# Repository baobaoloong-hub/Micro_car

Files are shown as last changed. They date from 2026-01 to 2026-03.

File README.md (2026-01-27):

# Micro_car
### gitee上传不了
#### 写在前面
前几个月抽了点时间画的车模，还想着再打一年，可惜要考研没时间，而且也没队友一起玩了，直接开源了,负压部分随便画的(效果挺好7w功率1.2kg+,同功率没见到比这个高的了),车模优化空间很大,自行探索,车模除了负压部分，不需要 3d 打印，所以车模很精致，而且挺稳定的，非常易上手
#⚠️注意⚠️
仅供参考，觉得不行的就当看个乐，毕竟我没下过地跑过，也希望有佬能参考做完，记得让我饱饱眼福，祝21届各位一路开挂，斩获佳绩，赛出风采！

#### 说明
1. 编码器测试过是可以的，`编码器磁铁和电机靠的有些近会有一些的小影响，自制编码器没什么难点，一个磁编码器芯片，需要输出方向正交编码器加个 d 触发器就可以了，可以试试英飞凌的 tle5012，e1000 版本的，出厂默认正交输出（手册好像写的 4096 线），也可以使用其他的比如 mt6835...

2. 电机选型(预留了10mm,12mm孔位,其他的自行修改)，没细找电机，直接无脑 030 ,最好是铷磁铁的，扭力要大（折线需要大扭力，尤其是直角，有时候跑不快，上限低大概率是电机没劲）,牛爷爷用的那个也挺好，就是略微有点重。有实力的佬挑战一下无刷，好盈 1625，一些蚊车电机，淘宝还有好多不知名的好电机，钞能力直接马克松冯哈勃，二手的不推荐,好多都是快坏了的

3. 裙边，材质自己挑，铁氟龙的看过学弟的，感觉偏硬，容易变形，没用过不评价,用过的可以说说，推荐那种大棚膜，2 平米 2.6 元，四舍五入就是白送！根本用不完，耐磨还有韧性不易形变，强推强推，还有就是贴膜，直接纳米胶，大块的铺，尽量铺宽一点，不要留缝防止漏气，可以参考我给的图片。

4. 负压...

5. 开启负压后车模变形，轮子出现外八问题，不一定要觉得是底板硬度不够，可以再上面加个支撑，这个支撑可以是你的 板子，也可以任何东西，参考我去年的车模结构，底板我有打过铝基板，单层正好能放开电源和三个电机的驱动，1.5mm 板很重，20g 整，有佬有空可以试试 1mm 或者换成普通的板子。还有，飞檐走壁不知道底盘是不是有点低，自行调整（我感觉没大问题）

6. 胎皮，省事直接买的成品，很好用，推荐一下牛爷爷的硅胶贴包海绵（牛爷爷群里有）和青山佬的世一胎皮，

7. 3d 打印部分，我用的竹子的 a1mini，打印部分只有扇叶和负压支架，一定要开圆孔补偿，可以轻松装上且扇叶不松动，想要减轻重量轮毂也可以打印。
关于负压电机的那个支架，可以改进一下，换成弹簧型那种，我看到过国外的鼠车并不是直接连接，好像因为扇叶动平衡不好，会震动，螺丝共振会松动，陀螺仪可能也会漂，有条件的陀螺仪也加一下减震柱，类似穿越机（可能有点多此一举），不过这些问题我还没有发现车模也没感觉到震动

8. 关于车模的测试，我是建议大家一步到位，能用碳板用碳板，不要用 3 d 打印，因为很多问题是当你换了稳定的材质才发现根本没那回事，尤其是负压和底板摩擦，一套碳板大概 40 左右甚至更低，不想花钱直接打 pcb 替代碳板（比赛哪有不花钱的）

9. 待补充...

#### 物料清单

| 物品  | 店铺 | 备注 | |
|----|---|---|---|
| 轮毂 | 叮叮玩具城 | 中径,店铺里款式颜色很多自行选择 |  https://e.tb.cn/h.7KCqEZDSIRYSRkK?tk=ES7zUhpZbzG |
| 胎皮 | 龙祥兴 | 硅胶套皮  | https://e.tb.cn/h.7KaQ1hg8XNjvOgW?tk=3CPaUhpYhlx  |
| 径向磁铁  | 年磁科技 |  径向!!!!!! | https://e.tb.cn/h.7KlAtBGKxQvzEUj?tk=V5gjUhpasUc  |
| 轴套 | 2*4*6 |  不是必须买 | |
| 尼龙柱 | 6或7  | 负压用  | |
| 防滑螺母m2 | | | |
| 0.5模齿轮 | 大家一起来数牙 , 玩具齿轮大全 , 自己打印 | 轮齿40,电机齿14(自行调整,加起来54就行) ||
| 碳板 | | | |  | |  |
| 法兰轴承*8 | | F682w1.5 | |  | | https://e.tb.cn/h.7KO1xlum2gcvA1G?tk=EAH1Uhp14ll |
| m2螺丝  | | 18,20,22(具体自行调整,有条件的直接钛合金 | |  | |  |
| 8520或8523 | | | |
| 六面螺母 | | 6*6*6  |  https://e.tb.cn/h.7KOXKpCuhlABRpd?tk=7vObUhpcHJm |
| ... | | | |

#### 安装说明

看着文件装吧.

#### 参与贡献

1.  Fork 本仓库
2.  新建 Feat_xxx 分支
3.  提交代码
4.  新建 Pull Request

#### 特技

1.  使用 Readme\_XXX.md 来支持不同的语言，例如 Readme\_en.md, Readme\_zh.md
2.  Gitee 官方博客 [blog.gitee.com](https://blog.gitee.com)
3.  你可以 [https://gitee.com/explore](https://gitee.com/explore) 这个地址来了解 Gitee 上的优秀开源项目
4.  [GVP](https://gitee.com/gvp) 全称是 Gitee 最有价值开源项目，是综合评定出的优秀开源项目
5.  Gitee 官方提供的使用手册 [https://gitee.com/help](https://gitee.com/help)
6.  Gitee 封面人物是一档用来展示 Gitee 会员风采的栏目 [https://gitee.com/gitee-stars/](https://gitee.com/gitee-stars/)

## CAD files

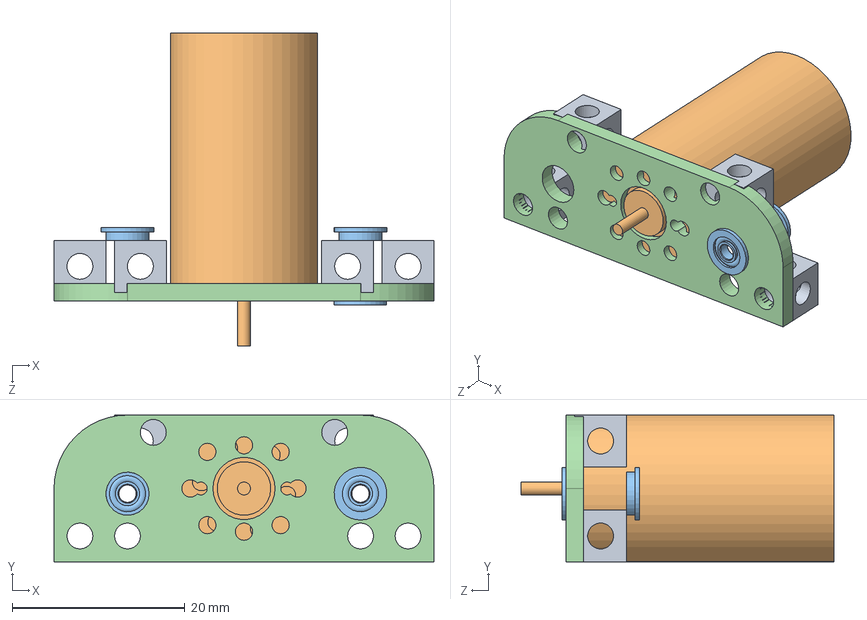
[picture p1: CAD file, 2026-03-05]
更新_看这个/侧轮整体.SLDASM
44.0 x 17.0 x 36.2 mm
侧板
F682-2Z 2×5×1.5_法兰轴承 x 3
六面螺母 x 4

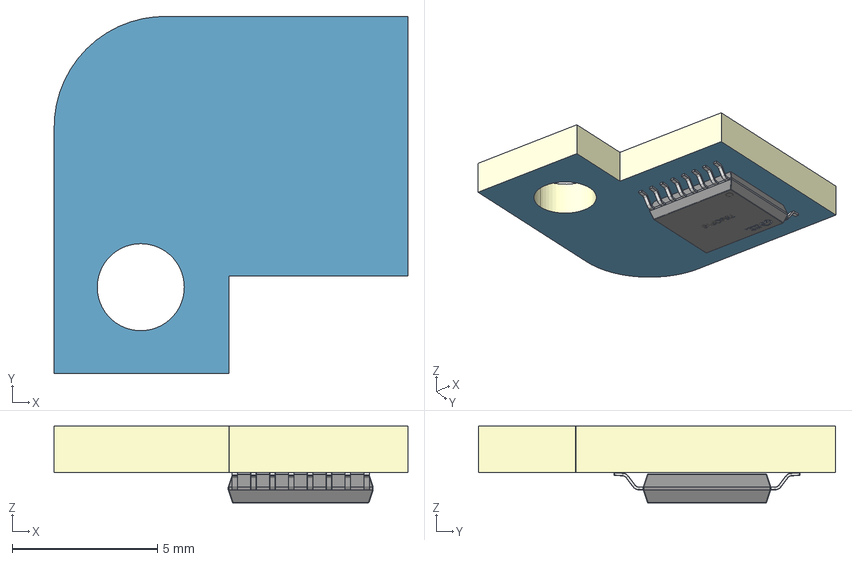
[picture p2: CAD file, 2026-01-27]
编码器.step
12.2 x 12.3 x 2.65 mm
Board~ZMgj
TopCopper~ZMgj
BottomCopper~ZMgj
TopFpcStiffener~ZMgj
BottomFpcStiffener~ZMgj
TSSOP-16_L5.0-W4.4-P0.65-LS6.4-BL~TSSOP-16_ L5.0-W4.4-H1.0-LS6.4-P0.65~ZMgj

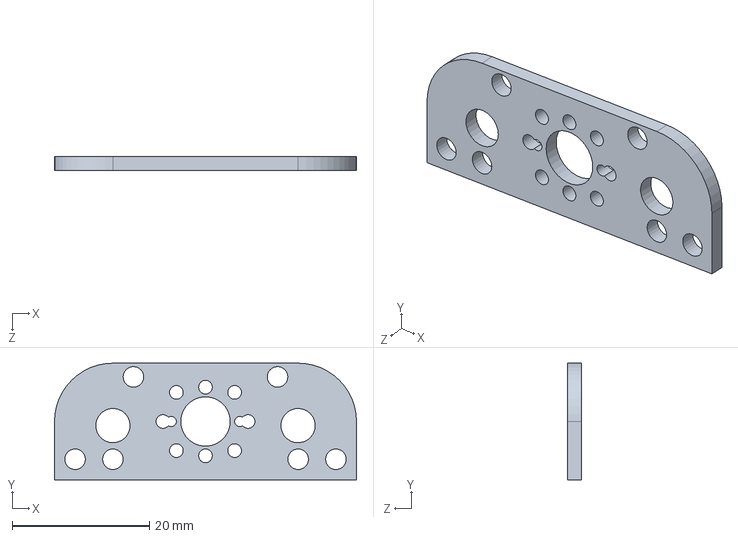
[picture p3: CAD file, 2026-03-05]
更新_看这个/侧板.SLDPRT
44.0 x 17.0 x 2.00 mm

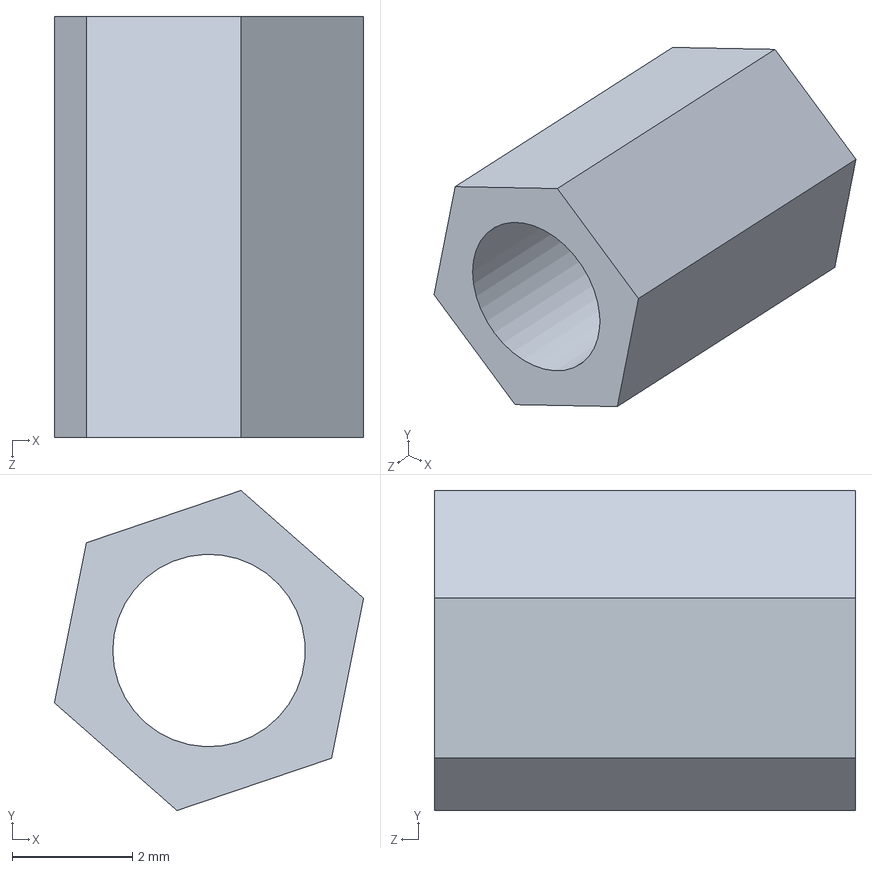
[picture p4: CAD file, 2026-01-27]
更新_看这个/铜柱7mm.SLDPRT
5.14 x 5.32 x 7.00 mm

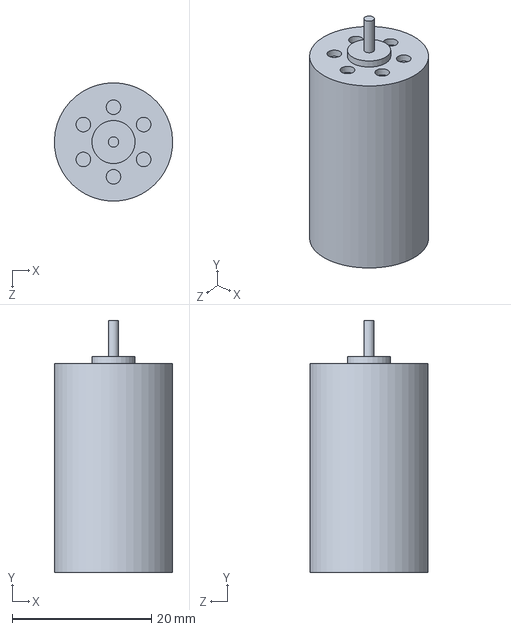
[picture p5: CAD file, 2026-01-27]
更新_看这个/1725.SLDPRT
17.0 x 36.2 x 17.0 mm

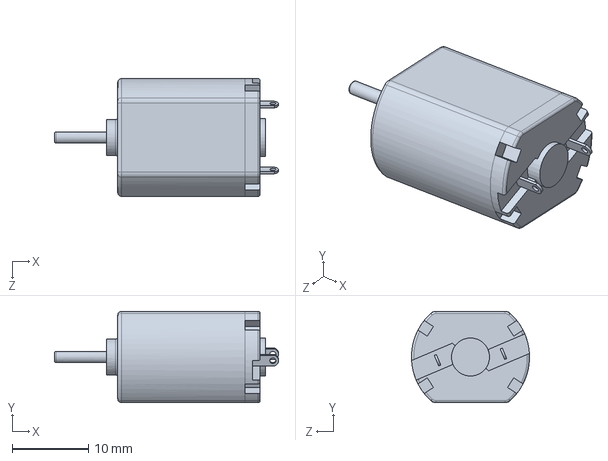
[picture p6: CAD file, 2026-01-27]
更新_看这个/Standard Motor 030.SLDPRT
29.4 x 12.0 x 15.5 mm

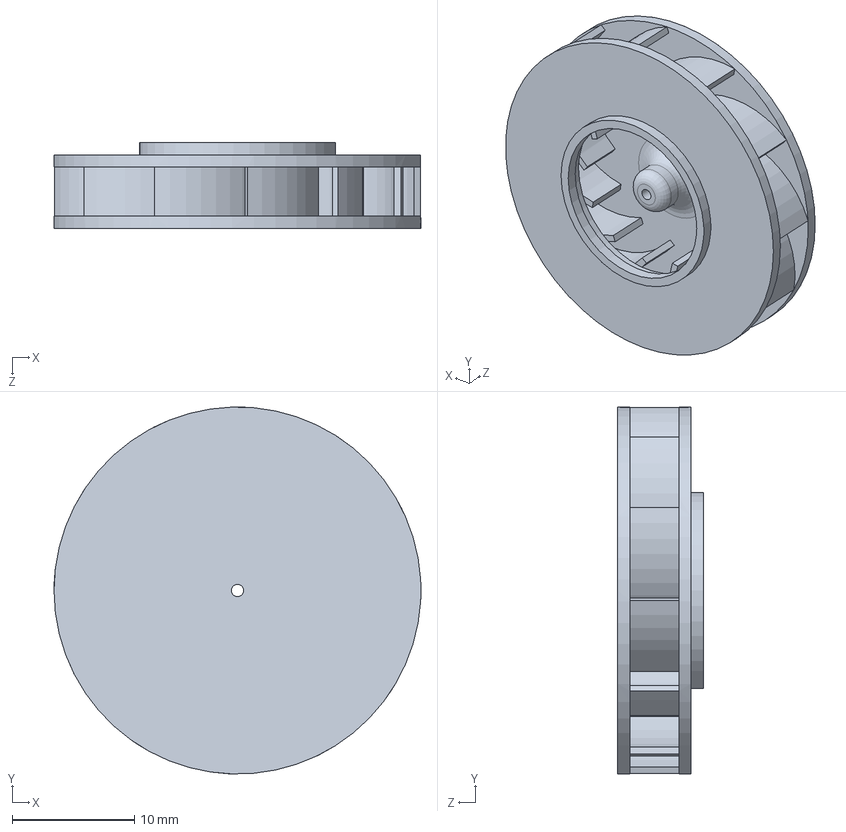
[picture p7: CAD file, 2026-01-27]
更新_看这个/扇叶 - 副本.SLDPRT
30.0 x 30.0 x 7.00 mm

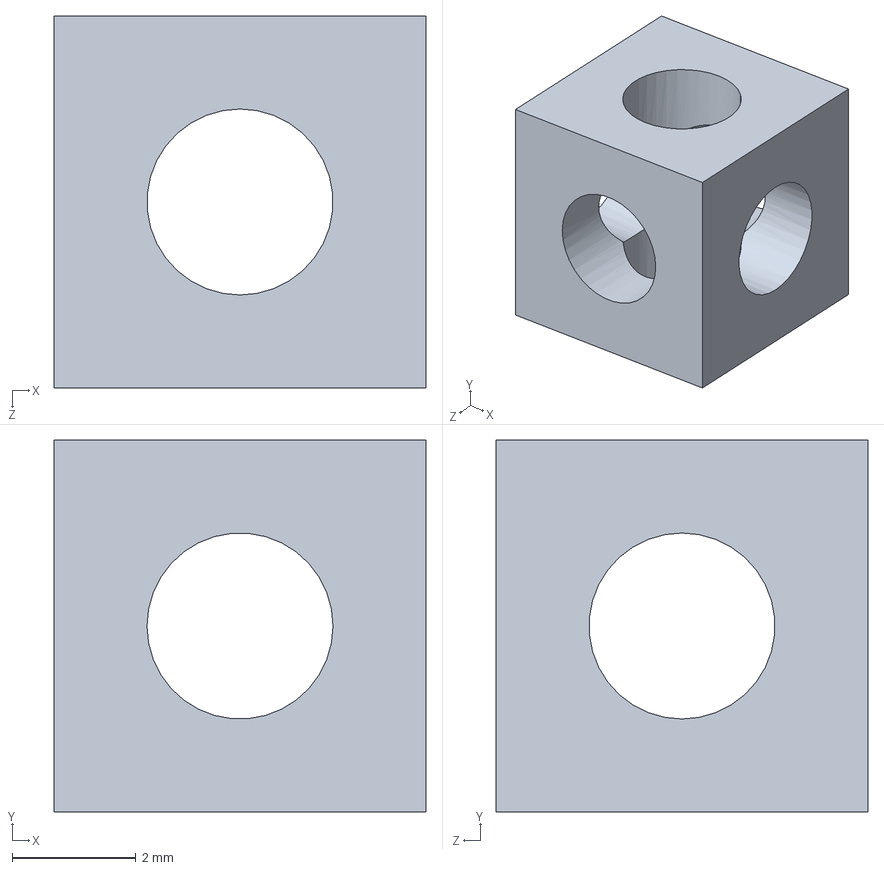
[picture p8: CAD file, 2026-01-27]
更新_看这个/六面螺母.SLDPRT
6.00 x 6.00 x 6.00 mm

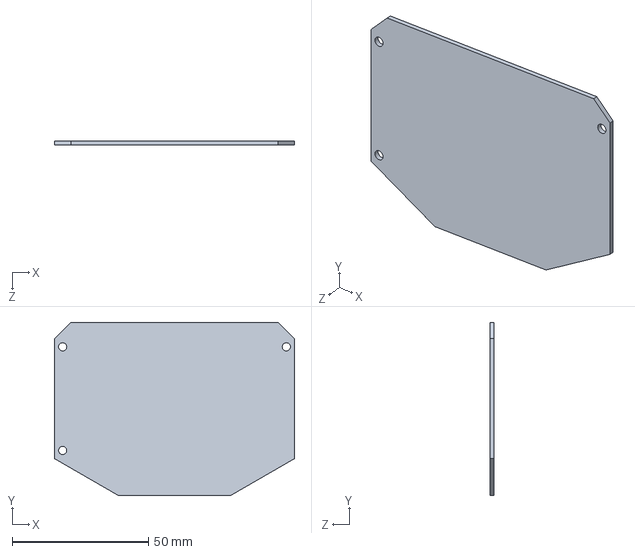
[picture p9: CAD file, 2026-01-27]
更新_看这个/底板.SLDPRT
88.0 x 63.6 x 1.50 mm

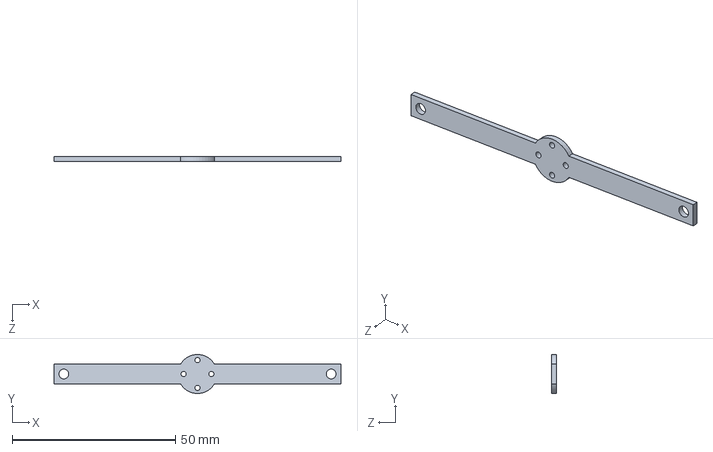
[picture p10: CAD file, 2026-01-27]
更新_看这个/负压支架.SLDPRT
88.0 x 12.0 x 1.50 mm

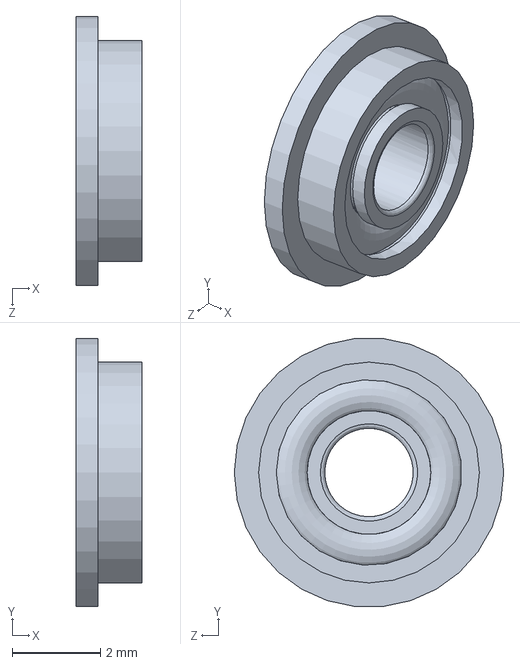
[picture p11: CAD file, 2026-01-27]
更新_看这个/F682-2Z 2×5×1.5_法兰轴承.SLDPRT
1.50 x 6.07 x 6.10 mm

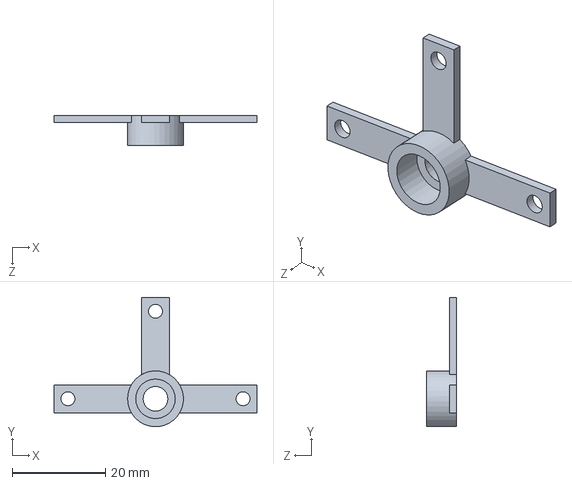
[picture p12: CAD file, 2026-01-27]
更新_看这个/8520支架 - 副本.SLDPRT
43.6 x 27.8 x 6.50 mm

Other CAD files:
更新_看这个/轮.SLDASM
更新_看这个/胎皮.SLDPRT
更新_看这个/零件1.SLDPRT
